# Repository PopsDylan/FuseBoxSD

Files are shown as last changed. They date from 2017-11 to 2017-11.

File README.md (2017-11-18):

# FuseBoxSD

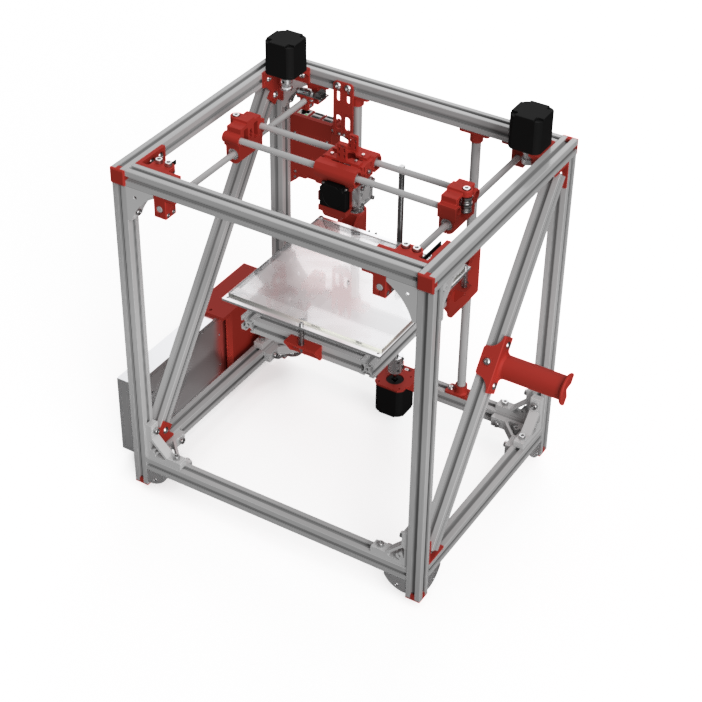
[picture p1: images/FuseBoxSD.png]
FuseBoxSD


The FuseBoxSD 3D printer is derived from the [FB2020 Plus by AxMod3DPrint](http://github.com/AxMod3DPrint/FB2020). 

Changes from the FB2020 Plus include
* Metal brackets replace printed brackets
* The carriage and idlers have been redesigned
* The printed parts for the bed have been modified to fit the heatbed
* Many of the other printed parts have been modified for M5 screws
* The controller runs Smoothieware
* A Raspberry Pi 3 is included, for OctoPi
* A complete model is provided, in Fusion 360 and STEP formats

You will need to provide a Bowden extruder. We have been using the [Belted Extruder v4 by dintid](http://www.thingiverse.com/thing:2527297).

Copyright PopsDylan 2017.

This documentation describes Open Hardware and is licensed under the CERN OHL v. 1.2.

You may redistribute and modify this documentation under the terms of the CERN OHL v.1.2. (http://ohwr.org/cernohl). This documentation is distributed WITHOUT ANY EXPRESS OR IMPLIED WARRANTY, INCLUDING OF MERCHANTABILITY, SATISFACTORY QUALITY AND FITNESS FOR A PARTICULAR PURPOSE. Please see the CERN OHL v.1.2 for applicable conditions.

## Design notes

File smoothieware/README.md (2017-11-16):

Flash the firmware.bin file from this folder, or download and flash the latest Smoothieware build from https://github.com/Smoothieware/Smoothieware/tree/edge/FirmwareBin. 

The config.txt file in this folder replaces the configuration file on your Azteeg X5 Mini board. Review the contents of the configuration file before you install it on the board.

Refer to the Smoothieware documentation (http://smoothieware.org/) for more information. The 3D Printer Guide (http://smoothieware.org/3d-printer-guide) will be helpful.

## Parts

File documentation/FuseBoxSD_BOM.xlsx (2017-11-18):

Quantity | Supplier | Part Number | Description
Electronics
1 | Delta Electronics | BFB03505HHA-A | FAN BLOWER 35X10MM 5VDC
1 | EPCOS | B84776A0004A000 | Power Entry Connector Receptacle, Male Blades - Module IEC 320-C14 Panel Mount, Flange
1 | Mean Well | LRS-350-24 | Switching Power Supply 350.4W 24V 14.6A 115Vac or 230Vac
2 | Omron | D2F-01FL-D3 | SWITCH SNAP ACTION SPDT 100MA
1 | Omron | D2HW_C201H | SWITCH SNAP ACTION SPDT 100MA 125V
1 | Panucatt | AX5MINI | Azteeg X5 mini 32BIT All-in-one Controller V3 with 4pcs SD5984 and vertical male header
1 | raspberrypi.org | Raspberry Pi 3 Model B | Raspberry Pi 3 Model B
1 | SMW3D | endstop | Makerbot-style mechanical endstop
1 | Various | Power Cord | IEC Power Cord
1 | Various | USB Cable | USB Mini B Cable
Aluminum Extrusion and Hardware
2 | Misumi | HFS5-2020-147 | 2020 Extrusion, 147mm
2 | Misumi | HFS5-2020-235 | 2020 Extrusion, 235mm
2 | Misumi | HFS5-2020-300 | 2020 Extrusion, 300mm
2 | Misumi | HFS5-2020-340 | 2020 Extrusion, 340mm
4 | Misumi | HFS5-2020-380 | 2020 Extrusion, 380mm
4 | Misumi | HFS5-2020-445 | 2020 Extrusion, 445mm
2 | Misumi | HFS5-2020-465 | 2020 Extrusion, 465mm
137 | Misumi | HNTT5-5 | Pre-Assembly Insertion Short Nut
4 | Misumi | HBLFSSW5-C | Reversal bracket with tab, 4 holes
8 | MIsumi | HBLFSNF5-C_b | Short Reversal Bracket
16 | Misumi | HBKUS5-C | Thick bracket with tab for 2020 extrusion
Hardware
16 | Fushi (aliexpress) | F695ZZ | F695ZZ Flange Bearing 5x13x4mm
4 | K&J Magnetics | D22 | Magnet 1/8" dia x 1/8" thick
22 | link cnc (aliexpress) | 5x8x1 | 5mm x 8mm x 0.5mm shim
18 | McMaster Carr | 91828A111 | M2 Hex Nut, Stainless Steel
2 | McMaster Carr | 93625A101 | M2 Locknut, Stainless Steel
6 | McMaster Carr | 91292A833 | M2x10mm Socket Head Screw, Stainless Steel
4 | McMaster Carr | 92095A455 | M2x12mm Hex Drive Rounded Head Screw, Stainless Steel
6 | McMaster Carr | 91292A013 | M2x20mm Socket Head Screw, Stainless Steel
4 | McMaster Carr | 92000A015 | M2x8mm Phillips Rounded Head Screw, Stainless Steel
20 | McMaster Carr | 91828A211 | M3 Nut, Stainless Steel
9 | McMaster Carr | 93625A100 | M3 Nylon-Insert Locknut, Stainless steel
3 | McMaster Carr | 91292A113 | M3x10mm Socket Head Screw, Stainless Steel
8 | McMaster Carr | 91292A114 | M3x12mm Socket Head Screw, Stainless steel
12 | McMaster Carr | 91292A027 | M3x14mm Socket Head Screw, Stainless Steel
4 | McMaster Carr | 91292A115 | M3x16mm Socket Head Screw, Stainless Steel
3 | McMaster Carr | 91292A123 | M3x20mm Socket Head Screw, Stainless Steel
3 | McMaster Carr | 91292A024 | M3x40mm Socket Head Screw, Stainless steel
6 | McMaster Carr | 91292A112 | M3x8mm Socket Head Screw, Stainless Steel
4 | McMaster Carr | 93625A200 | M5 Locknut, Stainless Steel
37 | McMaster Carr | 91292A124 | M5x10mm Socket Head Screw, Stainless Steel
32 | McMaster Carr | 91292A058 | M5x14mm socket head screw, stainless steel
2 | McMaster Carr | 91292A192 | M5x30mm Socket Head Screw, Stainless Steel
4 | McMaster Carr | 91292A193 | M5x35mm Socket Head Screw, Stainless Steel
68 | McMaster Carr | 92095A207 | M5x8mm hex drive rounded head screw, stainless steel
4 | McMaster Carr | 92871A047 | Unthreaded spacer 8mm OD, 10mm Long for M5 Screw Size, Stainless Steel
3 | SMW3D | LExt sprint | Light extruder spring
Heatbed
1 | PrintInZ | BG-3.3-200x213 | Borosilicate Glass Print Bed 213mm x 200mm x 3.3mm
1 | SMW3D | 100K 3950 | 100K NTC 3950 Thermistor
1 | SMW3D | MK3-ALU | MK3 Heatbed 219mm x 219mm
1 | E3D | E3D V6 | E3D V6 Hot End
Linear Motion
3 | Automation Technology | KL17H248-15-4A | NEMA-17 Stepper, 76 oz-in
2 | Misumi | SFU12-400 | Precision linear shaft, 12mm diameter, 400mm length
2 | Misumi | SFU8-340 | Precision linear shaft, 8mm diameter, 340mm length
1 | SMW3D | 5x8cplr | 5mm x 8mm Flexible Coupler
2 | SMW3D | GT2 20T, 5mm bore | GT2 20T 5mm bore, 6mm width pulley
2 | SMW3D | LM12LUU | Linear Bearing, 12mm inner diameter, 21mm outer diameter, 57mm length
4 | SMW3D | LM8LUU | Linear Bearing, 8mm inner diameter, 15mm outer diameter, 45mm length
2 | SMW3D | 8300 | Linear Shaft, 8mm diameter, 300mm length
2 | Various | GT2 Belt | GT2 Belt, 6mm width, 1.5m length
1 | Zyltech | 8m T8x2 Trapezoidal ACME Lead Screw | 8mm T8x2 lead screw, trapezoidal ACME, 300mm
1 | Zyltech | T8x2 8mm lead screw nut | Trapezoidal ACME 8mm lead screw nut, anit-backlash, single start 2mm pitch
Printed Parts
1 | Printed Part | 1_12mm_Bed_Carrier_Left_209mm
1 | Printed Part | 1_12mm_Bed_Carrier_Right_209mm
1 | Printed Part | 1_3_Point_Bed_Holder_209mm
1 | Printed Part | 1_Azteeg_X5_Mini_Bracket
1 | Printed Part | 1_Carriage
1 | Printed Part | 1_E3Dv6_Duct_Part_1
1 | Printed Part | 1_E3Dv6_Duct_Part_2
1 | Printed Part | 1_Fan_Duct
1 | Printed Part | 1_Left_Idler
1 | Printed Part | 1_Power_Supply_Housing
1 | Printed Part | 1_Right_Idler
1 | Printed Part | 1_RPI_Top
1 | Printed Part | 1_RPI3_Bottom
1 | Printed Part | 1_Spool_Hanger
1 | Printed Part | 1_Y_Endstop_Holder
1 | Printed Part | 1_Z_Endstop
1 | Printed Part | 1_Z_Leadscrew_Nut_Holder_Zyltech_T8x2
1 | Printed Part | 1_Z_Motor_Holder
1 | Printed Part | 1_Z_Probe
2 | Printed Part | 2_Belt_Clip
2 | Printed Part | 2_Motor_Holder
2 | Printed Part | 2_Wire_Guide
2 | Printed Part | 2_Y_Carrier
4 | Printed Part | 4_12mm_Z_Rod_Holder
4 | Printed Part | 4_Corner_Brace_Mount
4 | Printed Part | 4_Y_Rod_Holder
8 | Printed Part | 8_Foot_Endcap
Copyright PopsDylan 2017. This documentation describes Open Hardware and is licensed under the CERN OHL v. 1.2. You may redistribute and modify this documentation under the terms of the CERN OHL v.1.2. (http://ohwr.org/cernohl). This documentation is distributed WITHOUT ANY EXPRESS OR IMPLIED WARRANTY, INCLUDING OF MERCHANTABILITY, SATISFACTORY QUALITY AND FITNESS FOR A PARTICULAR PURPOSE. Please see the CERN OHL v.1.2 for applicable conditions.

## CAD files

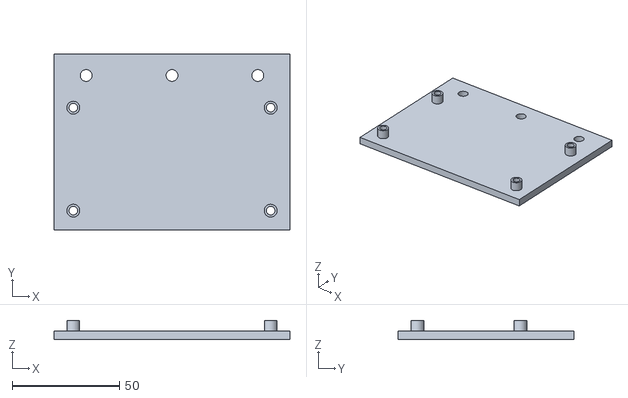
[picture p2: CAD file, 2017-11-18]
stl/1_Azteeg_X5_Mini_Bracket.stl
110.0 x 82.0 x 9.00

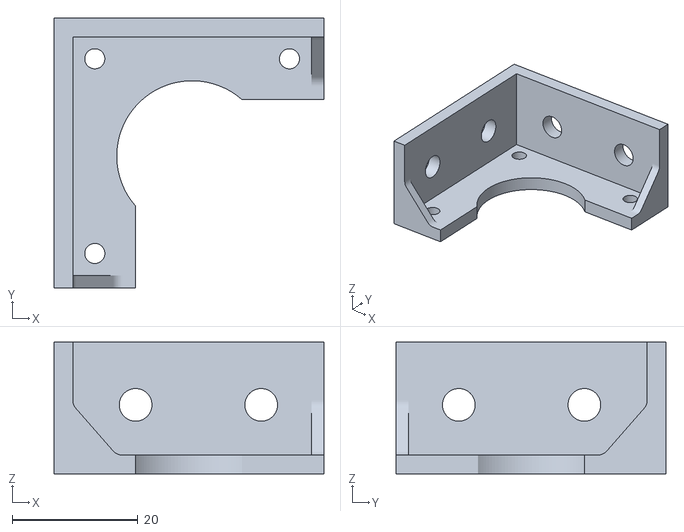
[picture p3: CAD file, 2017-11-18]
stl/2_Motor_Holder.stl
43.0 x 43.0 x 21.0

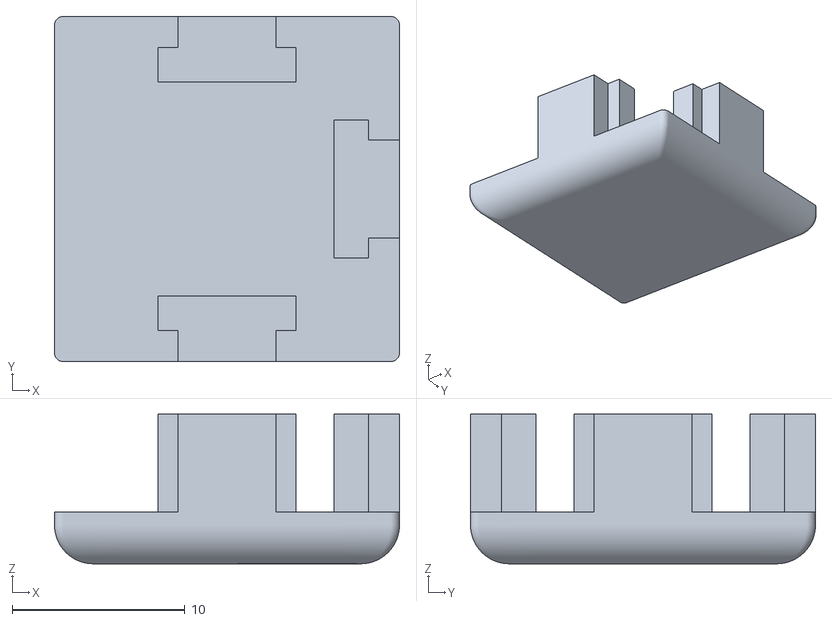
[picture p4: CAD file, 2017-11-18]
stl/8_Foot_Endcap.stl
20.0 x 20.0 x 8.67

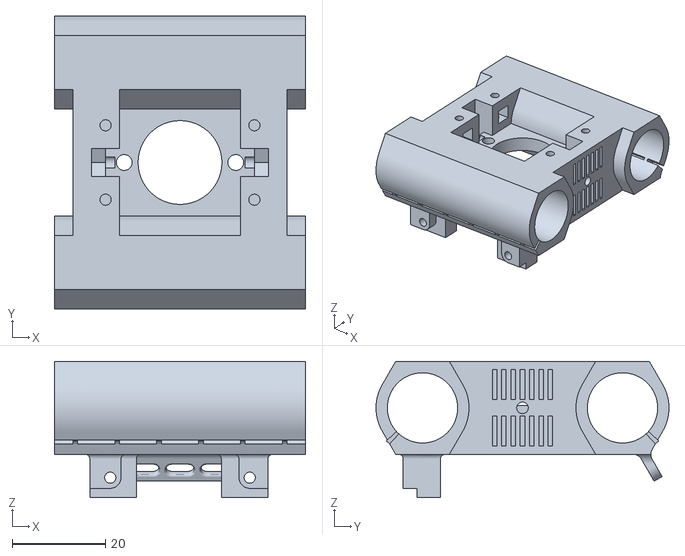
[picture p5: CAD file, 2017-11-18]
stl/1_Carriage.stl
54.0 x 63.0 x 29.3

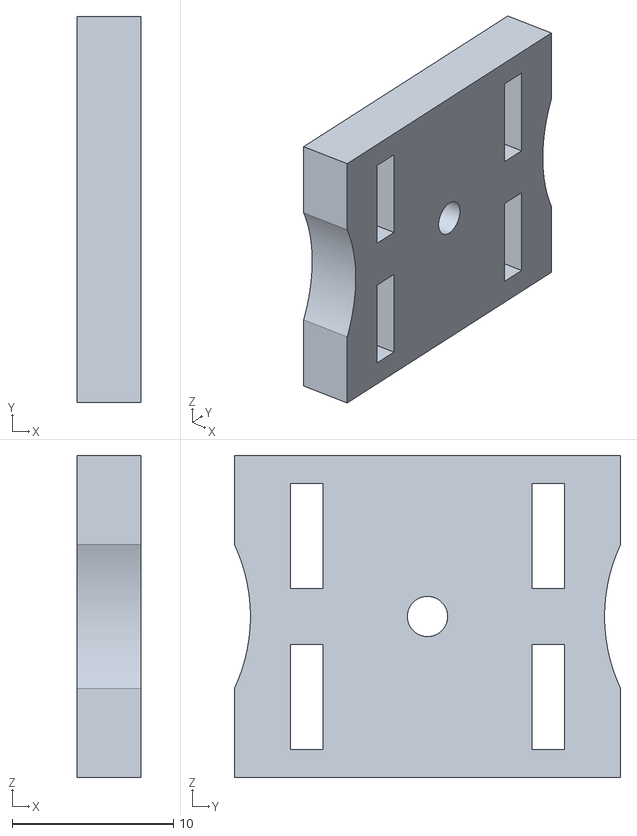
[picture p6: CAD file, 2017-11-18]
stl/2_Belt_Clip.stl
4.00 x 24.0 x 20.0

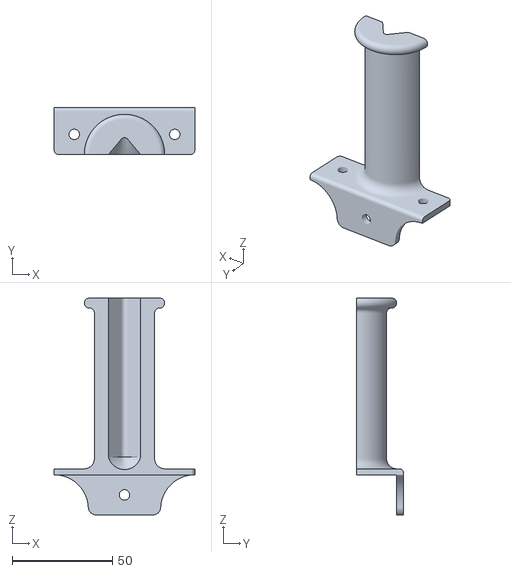
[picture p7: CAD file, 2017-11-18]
stl/1_Spool_Hanger.stl
70.0 x 23.4 x 108.0

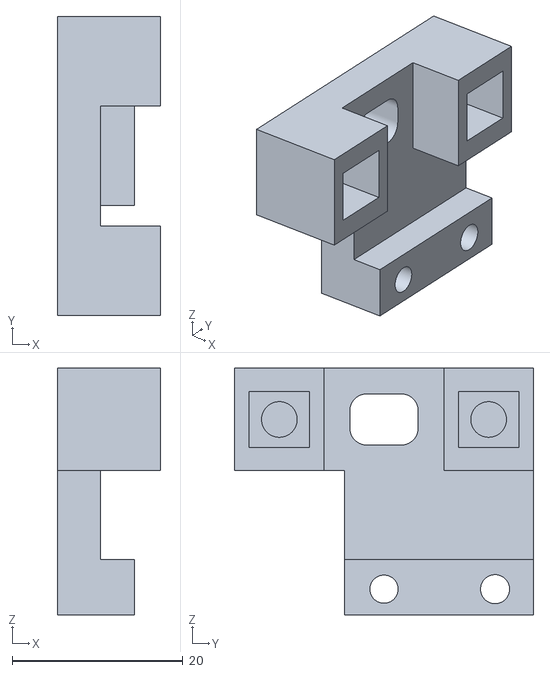
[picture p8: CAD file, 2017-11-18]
stl/1_Z_Probe.stl
12.0 x 35.0 x 28.9

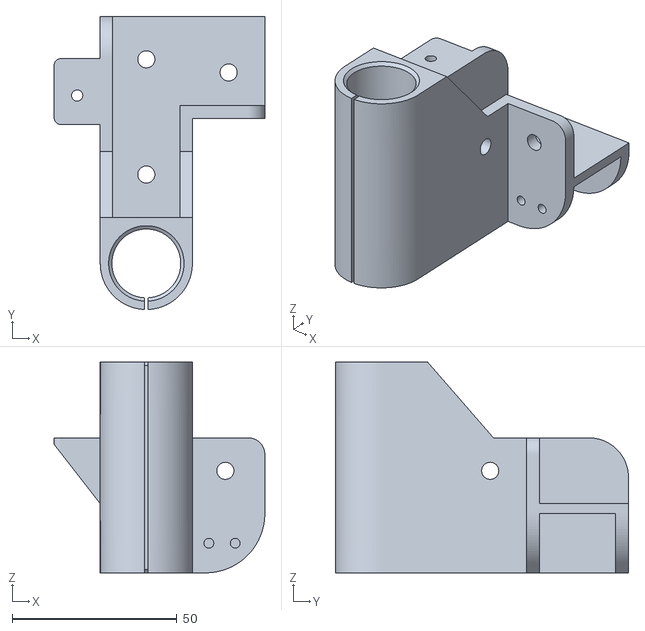
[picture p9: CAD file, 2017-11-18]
stl/1_12mm_Bed_Carrier_Right_209mm.stl
64.0 x 89.0 x 64.0

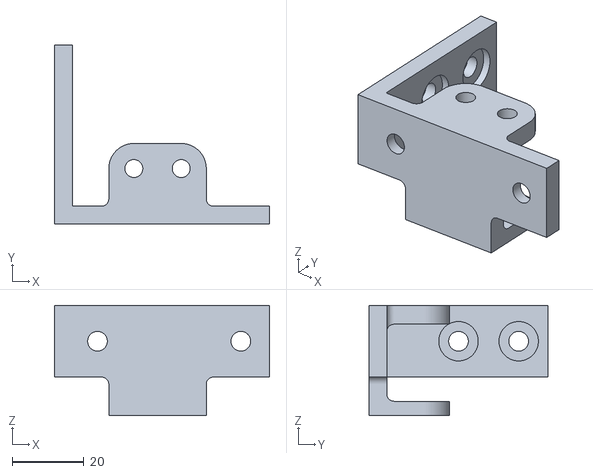
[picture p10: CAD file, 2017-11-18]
stl/1_Left_Idler.stl
60.0 x 50.0 x 30.8

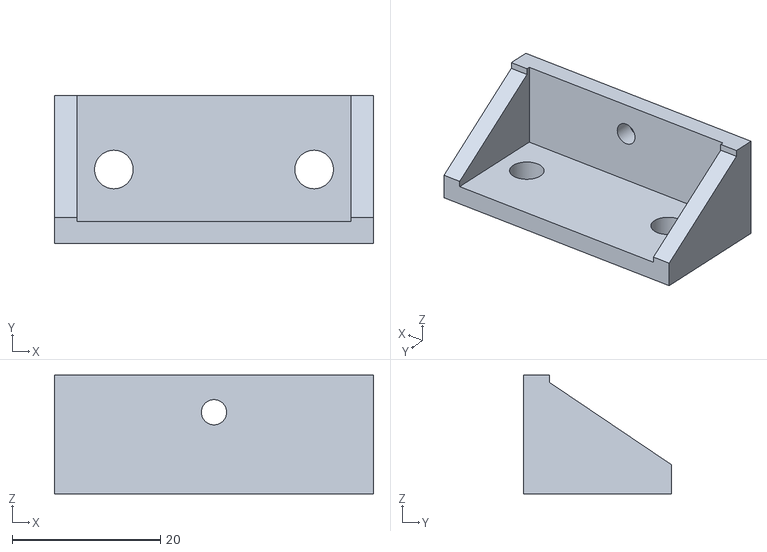
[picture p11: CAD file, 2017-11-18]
stl/1_3_Point_Bed_Holder_209mm.stl
43.0 x 20.0 x 16.0

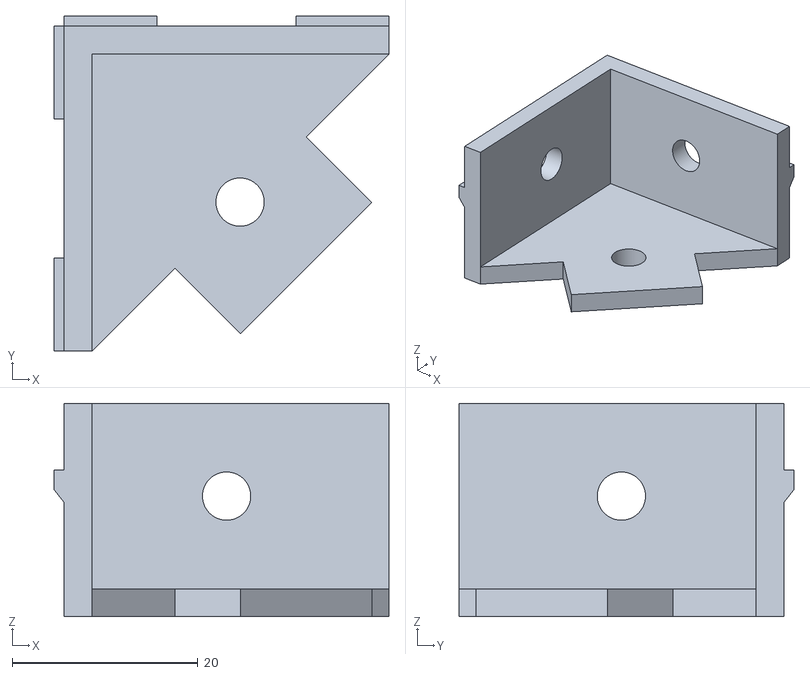
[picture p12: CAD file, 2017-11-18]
stl/4_Corner_Brace_Mount.stl
36.1 x 36.1 x 23.0

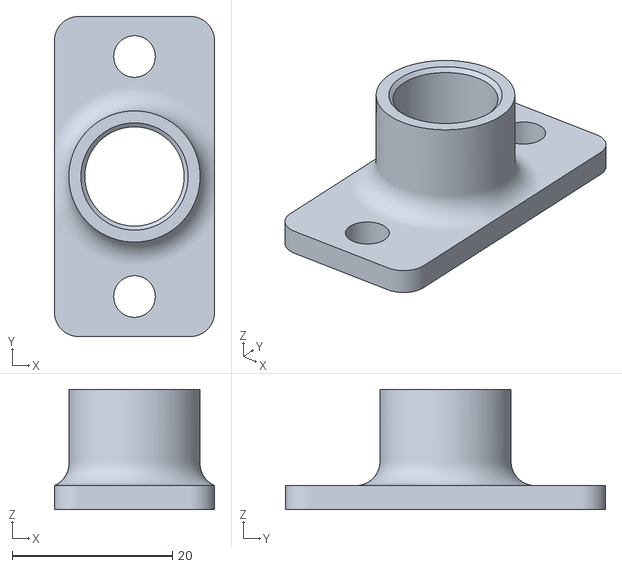
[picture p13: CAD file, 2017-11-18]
stl/4_12mm_Z_Rod_Holder.stl
20.0 x 40.0 x 15.0

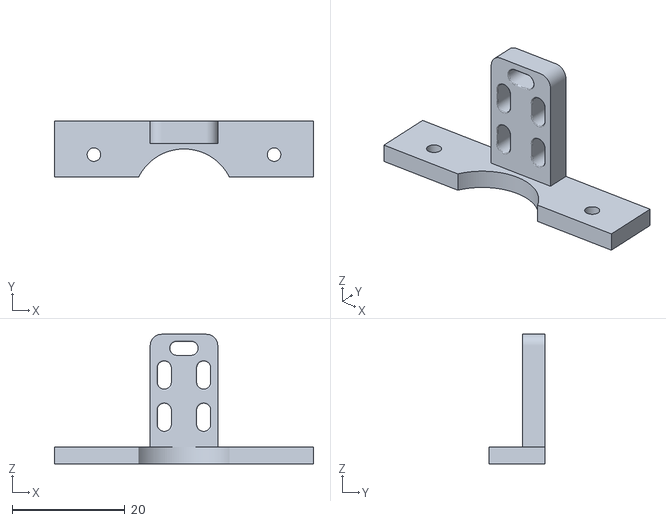
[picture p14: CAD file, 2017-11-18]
stl/2_Wire_Guide.stl
46.0 x 10.0 x 23.0

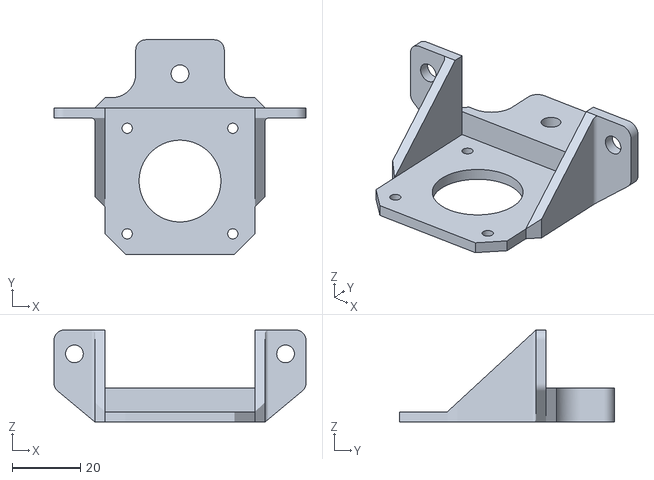
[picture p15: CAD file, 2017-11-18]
stl/1_Z_Motor_Holder.stl
74.0 x 63.0 x 27.0

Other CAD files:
stl/1_12mm_Bed_Carrier_Left_209mm.stl
stl/2_Y_Carrier.stl
stl/1_Power_Supply_Housing.stl
stl/1_Right_Idler.stl
stl/1_E3Dv6_Duct_Part_1.stl
stl/1_E3Dv6_Duct_Part_2.stl
stl/1_RPI3_Bottom.stl
stl/1_RPI_Top.stl
stl/1_Y_Endstop_Holder.stl
stl/1_Z_Endstop.stl
stl/1_Z_Leadscrew_Nut_Holder_Zyltech_T8x2.stl
stl/4_Y_Rod_Holder.stl

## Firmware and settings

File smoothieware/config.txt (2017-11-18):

# Robot module configurations : general handling of movement G-codes and slicing into moves
default_feed_rate                            4000             # Default rate ( mm/minute ) for G1/G2/G3 moves
default_seek_rate                            4000             # Default rate ( mm/minute ) for G0 moves
mm_per_arc_segment                           0.5              # Arcs are cut into segments ( lines ), this is the length for these segments.  Smaller values mean more resolution, higher values mean faster computation
#mm_per_line_segment                          5                # Lines can be cut into segments ( not usefull with cartesian coordinates robots ).

# Arm solution configuration : Cartesian robot. Translates mm positions into stepper positions
arm_solution                                 corexy			  
alpha_steps_per_mm                           160               # Steps per mm for alpha stepper
beta_steps_per_mm                            160               # Steps per mm for beta stepper
gamma_steps_per_mm                           3200               # Steps per mm for gamma stepper

# Planner module configuration : Look-ahead and acceleration configuration
planner_queue_size                           32               # DO NOT CHANGE THIS UNLESS YOU KNOW EXACTLY WHAT YOUR ARE DOING
acceleration                                 3000             # Acceleration in mm/second/second.
#z_acceleration                              500              # Acceleration for Z only moves in mm/s^2, 0 disables it, disabled by default. DO NOT SET ON A DELTA
junction_deviation                           0.05             # Similar to the old "max_jerk", in millimeters, see : https://github.com/grbl/grbl/blob/master/planner.c#L409
                                                              # and https://github.com/grbl/grbl/wiki/Configuring-Grbl-v0.8 . Lower values mean being more careful, higher values means being faster and have more jerk

# Stepper module configuration
microseconds_per_step_pulse                  1                # Duration of step pulses to stepper drivers, in microseconds
base_stepping_frequency                      100000           # Base frequency for stepping

# Stepper module pins ( ports, and pin numbers, appending "!" to the number will invert a pin )
alpha_step_pin                               2.1              # Pin for alpha stepper step signal
alpha_dir_pin                                0.11             # Pin for alpha stepper direction
alpha_en_pin                                 0.10            # Pin for alpha enable pin
alpha_current                                1.3              # X stepper motor current
x_axis_max_speed                             30000            # mm/min
alpha_max_rate                               30000.0          # mm/min actuator max speed

beta_step_pin                                2.2              # Pin for beta stepper step signal
beta_dir_pin                                 0.20             # Pin for beta stepper direction
beta_en_pin                                  0.19            # Pin for beta enable
beta_current                                 1.3              # Y stepper motor current
y_axis_max_speed                             30000            # mm/min
beta_max_rate                                30000.0          # mm/min actuator max speed

gamma_step_pin                               2.3              # Pin for gamma stepper step signal
gamma_dir_pin                                0.22             # Pin for gamma stepper direction
gamma_en_pin                                 0.21            # Pin for gamma enable
gamma_current                                1.3              # Z stepper motor current
z_axis_max_speed                             300              # mm/min
gamma_max_rate                               300.0            # mm/min actuator max speed

# Serial communications configuration ( baud rate default to 9600 if undefined )
uart0.baud_rate                              115200           # Baud rate for the default hardware serial port
second_usb_serial_enable                     false            # This enables a second usb serial port (to have both pronterface and a terminal connected)

#msd_disable                                 false            # disable the MSD (USB SDCARD) when set to true
#leds_disable                                true             # disable using leds after config loaded
#dfu_enable                                  false            # for linux developers, set to true to enable DFU
#watchdog_timeout                            10               # watchdog timeout in seconds, default is 10, set to 0 to disable the watchdog


## Extruder module configuration
extruder.hotend.enable                          true             # Whether to activate the extruder module at all. All configuration is ignored if false
# use this value for MK8 extruder
#extruder.hotend.steps_per_mm                    281.707          # Steps per mm for extruder stepper
# use this value for belted extruder with 20-GT2 + 60-GT2 + 1/32 microstepping + 0.9 degree motor + E3D hobbed bolt
#extruder.hotend.steps_per_mm                  1662.40              # 
# use this value for V4 belted extruder with 20-GT2 + 60-GT2 + 1/32 microstepping + 0.9 degree motor + E3d hobbed bolt
extruder.hotend.steps_per_mm                  1637.99               #
extruder.hotend.default_feed_rate               600              # Default rate ( mm/minute ) for moves where only the extruder moves
extruder.hotend.acceleration                    500              # Acceleration for the stepper motor mm/sec²
extruder.hotend.max_speed                       50               # mm/s

extruder.hotend.step_pin                        2.0              # Pin for extruder step signal
extruder.hotend.dir_pin                         0.5              # Pin for extruder dir signal
extruder.hotend.en_pin                          0.4              # Pin for extruder enable signal


#use this value for larger stepper motor
#delta_current                                1.3                 # Extruder stepper motor current
#use this value for pancake stepper motor
delta_current                                 1.0               # Extruder stepper motor current

# Laser module configuration
laser_module_enable                          false            # Whether to activate the laser module at all. All configuration is
                                                              # ignored if false.
#laser_module_pin                             2.5             # this pin will be PWMed to control the laser. Only P2.0 - P2.5, P1.18, P1.20, P1.21, P1.23, P1.24, P1.26, P3.25, P3.26
                                                              # can be used since laser requires hardware PWM
#laser_module_maximum_power                   1.0             # this is the maximum duty cycle that will be applied to the laser
#laser_module_minimum_power                   0.0             # This is a value just below the minimum duty cycle that keeps the laser
                                                              # active without actually burning.
#laser_module_default_power                   0.8             # This is the default laser power that will be used for cuts if a power has not been specified.  The value is a scale between
                                                              # the maximum and minimum power levels specified above
#laser_module_pwm_period                      20              # this sets the pwm frequency as the period in microseconds

# Hotend temperature control configuration
temperature_control.hotend.enable            true             # Whether to activate this ( "hotend" ) module at all. All configuration is ignored if false.
temperature_control.hotend.thermistor_pin    0.24             # Pin for the thermistor to read
temperature_control.hotend.heater_pin        2.5              # Pin that controls the heater
temperature_control.hotend.thermistor        Semitec        # see http://smoothieware.org/temperaturecontrol#toc5
#temperature_control.hotend.beta             4066             # or set the beta value

temperature_control.hotend.set_m_code        104              #
temperature_control.hotend.set_and_wait_m_code 109            #
temperature_control.hotend.designator        T                #
temperature_control.hotend.max_pwm           200              #
#temperature_control.hotend.max_temp         300              # Set maximum temperature - Will prevent heating above 300 by default
#temperature_control.hotend.min_temp         0                # Set minimum temperature - Will prevent heating below 0 by default
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

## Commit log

2017-11-16 Add cables to model.
2017-11-18 Add STLs
    [1_12mm_Bed_Carrier_Left_209mm.stl, 1_12mm_Bed_Carrier_Right_209mm.stl, 1_3_Point_Bed _Holder_209mm.stl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]
2017-11-18 rename STL file
    [1_3_Point_Bed_Holder_209mm.stl]
2017-11-18 renamed STL file
    [1_3_Point_Bed _Holder_209mm.stl]
2017-11-18 Add BOM
    [FuseBoxSD_BOM.xlsx]
2017-11-18 Add Smoothieware FIRMWARE.BIN and config.txt
    [config.txt]
2017-11-18 Add information about the printer
